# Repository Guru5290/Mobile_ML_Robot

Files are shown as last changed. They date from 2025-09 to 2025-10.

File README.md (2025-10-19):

Project for [Robotics Dojo 2025](https://roboticsdojo.github.io/competition2025.html). A few mods to Josh Newans' articubot_one project documented on [github](https://github.com/joshnewans/articubot_one) and [youtube](https://www.youtube.com/playlist?list=PLunhqkrRNRhYAffV8JDiFOatQXuU-NnxT). 

# Quick Links
* [Sources](#sources)
* [Hardware Configuration](#hardware-configuration)
* [Software Dependencies](#software-dependencies)
* [Modified Parameters](#modified-parameters)
    * [Note](#note)
    * [Note on Localization](#note-on-localization)
* [Usage](#usage)
    * [Prerequisites](#preliminary)
    * [Simulation](#simulation)
    * [Real Robot](#real-robot)
    
* [Misc.](#misc)
* [Future](#future)

# Sources
- Simulation world obtained from the stl file sent by Lenny Ng'ang'a by converting it to a COLLADA file and importing it in Gazebo Fortress then saving it with the robot spawned in it. `src/jkl/worlds/GF.sdf`
- Map evaluation script obtained from [Dr. Shohei Aoki's repo](https://github.com/shohei/Map_Evaluation)
- diffDriveArduino from [RedstoneGithub's fork](https://github.com/RedstoneGithub/diffdrive_arduino) of Josh's diffdrive arduino
- [sllidar](https://github.com/Slamtec/sllidar_ros2) and [rplidar](https://docs.ros.org/en/ros2_packages/humble/api/rplidar_ros/) from those links
- [joy tester](https://github.com/joshnewans/joy_tester) is from Josh
- [serial](https://github.com/joshnewans/serial) is from Josh
- [serial_motor_demo](https://github.com/joshnewans/serial_motor_demo) is from Josh
- [rosArduinoBridge](https://github.com/joshnewans/ros_arduino_bridge) is Josh's fork of [hrobotics work](https://github.com/hbrobotics/ros_arduino_bridge)
  
Our [technical design paper](Technical%20paper%20Team_1%20Knights%20RDJ%202025.pdf), [technical presentation slides](Robotics%20Dojo%202025%20Knights%20Presentation.pdf), and [project poster](knights_poster%20RDJ%202025.pdf) may have a few more details on this project.

# Hardware Configuration
- Raspberry Pi running Ubuntu 22.04, dev machine running Ubuntu 22.04
- RPLidar A1 M8 connected to Pi via USB
- STM32F401 running [ROSArduinoBridge.ino](arduino-code/ROSArduinoBridge/ROSArduinoBridge.ino), connected to Pi USB
- 4 200 RPM motors with built-in encoders, with the encoders connected as shown in [encoder_driver.h](arduino-code/ROSArduinoBridge/encoder_driver.h)
- DRV8833 motor driver, with motor controls connected as shown in [motor_driver.h](arduino-code/ROSArduinoBridge/motor_driver.h)
- MPU6050 over I2C. The arduino sketch enables the DMP for great IMU performance. Also, a calibration sketch is provided by the [electronic cats library](https://github.com/ElectronicCats/mpu6050/wiki). This improved accuracy greatly.
- MG996R servo motor for bed actuation

Here's the bot [here](1L9A4192.JPG), [here](IMG_6601.jpeg)
Here's a simple  overview of the circuit. 
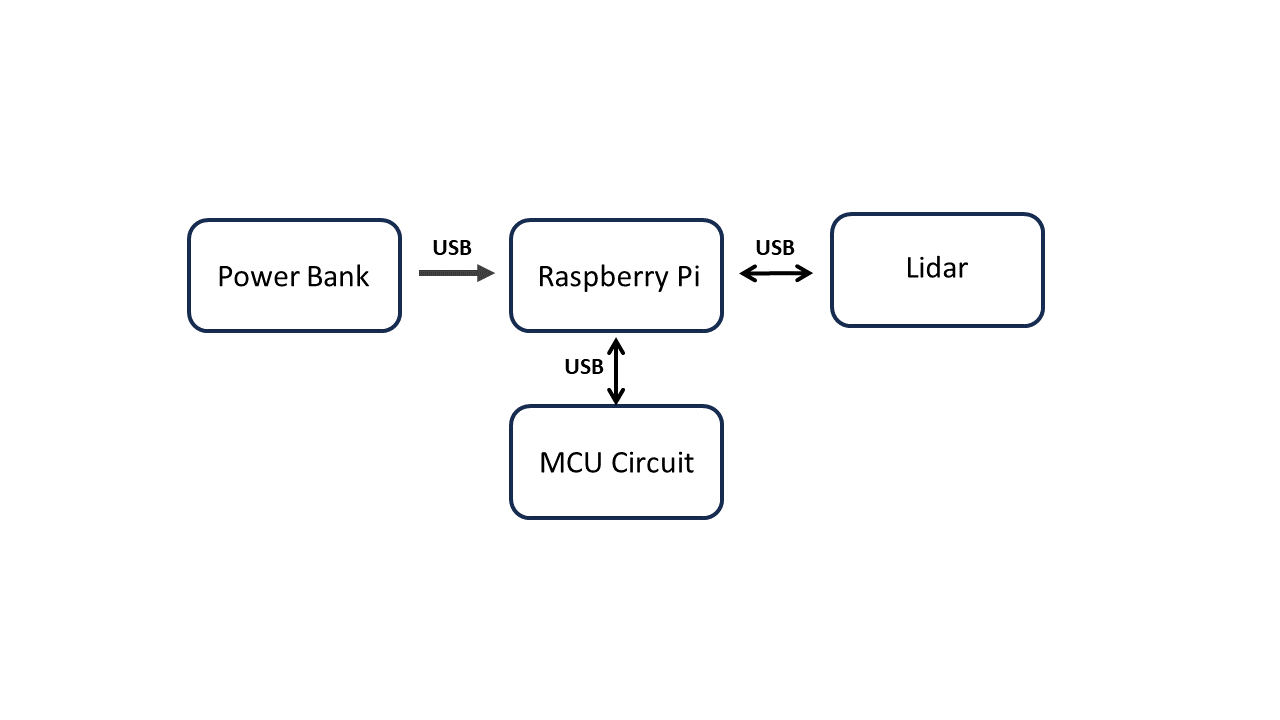
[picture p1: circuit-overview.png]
circuit overview


[This pdf](MCU-circuit.pdf) shows the MCU circuit in detail. The STM32 ships with a USB bootloader, allowing programming using DFU over usb. The configuration used in Arduino IDE is as below, STM32 boards can be added using this URL [https://github.com/stm32duino/BoardManagerFiles/raw/main/package_stmicroelectronics_index.json](https://github.com/stm32duino/BoardManagerFiles/raw/main/package_stmicroelectronics_index.json):
```
board manager entry - STM32 Based Boards by STMicroelectronics 
board - generic stm32f4 series
board part number - blackpill F401CC
Upload method - STM32Cube DFU
USB support - generic CDC Serial supercede U(S)ART
```

It is important to avoid using pins PA8-PA12. They're shown in blue on [the pinout diagram](STM32F401-pinout.jpg). These 5 pins have USB alternate functions and so misbehave when used as GPIO. Emphasis on PA11 (USB D-) and PA12 (USB D+). If you somehow get stuck unable to program the MCU over USB, you can recover by uploading a blank sketch using an FTDI, or ST-Link. 

# Software Dependencies
- Ubuntu 22.04 - ROS2 Humble pair was used here. Docker on windows is not recommended by us because of network woes. The WSL network is isolated from the system network, so ROS on Pi does not communicate with ROS on Docker by default. We were not able to get it working in time. Apart from that, native Ubuntu has way higher performance.
- twist-mux, ros-humble-teleop-twist-keyboard, ros-humble-teleop-twist-joy, slam-toolbox, ros-humble-navigation2, ros-humble-nav2-bringup, ros-humble-gazebo-ros-pkgs, ros-humble-xacro, ros-humble-ros2-control, ros-humble-rplidar-ros, ros-humble-robot-localization
<!-- - ros-humble-gazebo on pc -->
- tmux is not recommended, it was laggy on the Pi over SSH over wifi

# Modified Parameters
## src/jkl/description
### robot.urdf.xacro
The URDF was built using simple shapes. URDF using meshes was attempted [see knight.xacro](pi-code/src/jkl/description/urdf/knight.xacro). The benefit was the mesh was derived from the actual CAD of the robot. However, it was too laggy to update pose, etc. It was suspected that computing collisions using meshes was the cause, hence the creation of the [current URDF](pi-code/src/jkl/description/urdf/simple.xacro). 

Important to note is that the IMU on the actual robot was mounted such that X and Y axes did not match the X and Y axes of the robot. Also please note that for this manufacturer the axes drawn on the module are actually -X and -Y. Verify with your IMU's raw data if you plan to replicate this

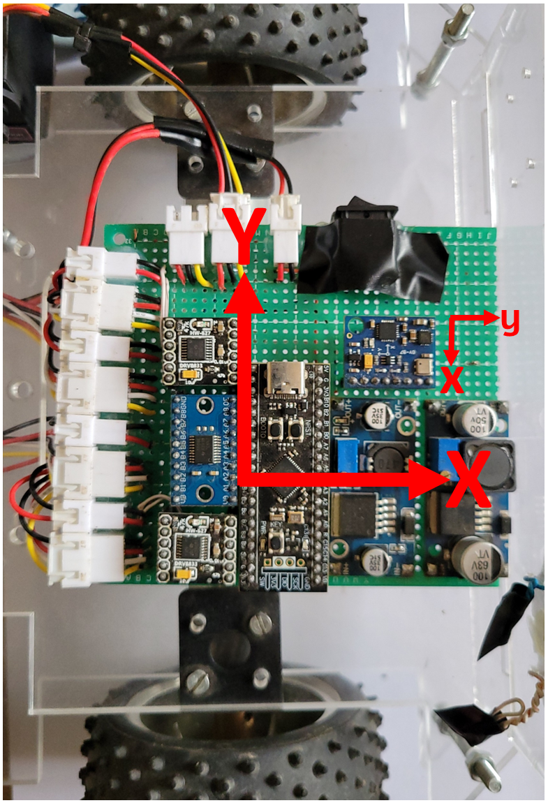
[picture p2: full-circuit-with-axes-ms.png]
full circuit with axes


So in the URDF, the IMU was rotated about the Z axis to match. This also affects the [EKF configuration file](#ekfyaml): we fuse the Y acceleration instead of X because Y is our axis of interest i.e. robot-forward axis. A justifiable assumption is that the imu_link->...->base_link TF's would account for this behind the scenes with the robot_localization package but no it does not at the time of writing. 
Had this been foreseen, the IMU would have been mounted x on X and y on Y. 

The URDF features an offset value for the centre of rotation. When the robot spins in place, it rotates about `base_link` (because the odom TF is odom->base_link). Therefore, it is important to match the centre of rotation of the real robot (or gazebo simulated robot) with the centre of rotation in Rviz. That's the role of `centre_of_rot_offset_x`. Getting this value right greatly improves odometry: when you set the fixed frame to odom in rviz, the laser frame will not drift. 

### gazebo_control.xacro (although not used)
```xml
<wheel_separation>0.207</wheel_separation>
<wheel_radius>0.0425</wheel_radius>
```

### ros2_control.xacro
```xml
<!-- stm32 -->
<param name="device">/dev/serial/by-id/usb-STMicroelectronics_BLACKPILL_F401CC_CDC_in_FS_Mode_206734803156-if00</param> 
<param name="baud_rate">57600</param>
<param name="enc_counts_per_rev">988</param>
```

## src/jkl/config/
### mapper_params_online_async.yaml
```yaml
loop_search_maximum_distance: 6.0 # (default is 3.0). The default value causes the robot to "teleport" during mapping, ruining a good map
```

### nav2_params.yaml
- initial_pose (not defined by default). Helps save time when using localization. A new pose can be given using rviz. Use it by having the odom reset (relaunching launch_robot) then launching online_async.launch.py. Then set the initial pose as 0 0 0
- controller_server: [mppi controller server](https://docs.nav2.org/configuration/packages/configuring-mppic.html) was used (dwb is default). rpp, teb and grace might have worked better, but mppi worked best out of the box
- controller server loop rate 15 Hz to minimize console spamming "control loop missed its 30Hz update rate"
- local_costmap & global_costmap: resolution: 0.02 (0.05 is default). Seems to get robot get stuck less frequently
- local_costmap: footprint used instead of radius, coz the robot is a polygon. Sized just over the robot's size
- global_costmap: radius retained, perhaps less compute intensive than footprint?
- amcl laser_max_range and min_range 12.0 and 0.3 respectively (default is )
- velocity smoother feedback: "CLOSED_LOOP" (default is OPEN_LOOP)
- velocity smoother velocities and accelerations: [0.35, 0.0, -0] and [12.5, 0.0, 8.2] (default are something else) The accelerations are very large. Something better should be identified and used
- [The docs](https://docs.nav2.org/tuning/index.html#inflation-potential-fields) recommends inflation radii that create **smooth** potential fields in the global and local costmaps. However, in testing, it was observed that having overlapping potentials (such as on corridors and parking spots) would cause the robot to fail passing as expected, even though a path had been planned. So the inflation radii were reduced until there was a little empty space in both costmaps at the narrowest corridor of the gamefield. 

We tried using the [theta-star planner](https://docs.nav2.org/configuration/packages/configuring-thetastar.html) instead of the default navfn. The robot plans are shorter and straighter, fixing the weaving issue we had last year. However, the plans hug the inflation radius too closely, causing navigation around simple corners to fail in a manner similar to that observed when the potential fields overlap. With time, perhaps that can be tuned out?

### my_controllers.yaml
For diff_cont
```yaml
wheel_separation: 0.207
wheel_radius: 0.0425
wheels_per_side: 2
odom_frame_id: odom
enable_odom_tf: false # crucial for EKF
```

These fields were added to provide hardware interfaces to the servo and IMU and 2 more wheels
```yaml
controller_manager:
  ros__parameters:
    # existing diff_cont

    # joints doubled for joint_broad
    joint_broad:
      type: joint_state_broadcaster/JointStateBroadcaster
      joints: ['front_left_joint', 'front_right_joint', 'back_left_joint', 'back_right_joint']
    
    imu_broadcaster:
      type: imu_sensor_broadcaster/IMUSensorBroadcaster # https://control.ros.org/humble/doc/ros2_controllers/imu_sensor_broadcaster/doc/userdoc.html

    servo_controller:
      type: position_controllers/JointGroupPositionController # https://control.ros.org/humble/doc/ros2_controllers/position_controllers/doc/userdoc.html

imu_broadcaster:
  ros__parameters:
    sensor_name: imu_sensor # specified in HW interface
    frame_id: imu_link

servo_controller:
  ros__parameters:
    joints:
      - servo # specified in HW interface
```

It is critical that enable_odom_tf in diff_cont should be false because ros2_control should not publish the odom->base_link transform. That role should be done by the EKF node. 

### ekf.yaml
[This config file](pi-code/src/jkl/config/ekf.yaml) is for sensor fusion using the [robot_localization](https://docs.ros.org/en/noetic/api/robot_localization/html/configuring_robot_localization.html) package. The configuration was largely based on the DOCS with one difference: The IMU on the robot was rotated 90 degrees about X axis wrt to the robot axes. So in order to fuse the acceleration along X axis, we actually fuse the reported acceleration of Y axis. 
#### Notes
* `publish_tf` is true. This is because ros2_control is no longer publishing the tf. 
* `imu0_relative` is true. We are only interested in the change in angular rotation about Z, not absolute angle value. Otherwise the orientation in RVIZ will be inconsistent per-run
* `imu0_remove_gravitational_acceleration` is true, the IMU reports absolute accelerations without subtracting gravity

## src/jkl/launch/
### rplidar.launch.py
The rplidar_ros launch file for A1 was copied and these fields were modified
```python
serial_port = LaunchConfiguration('serial_port', default='/dev/serial/by-id/usb-Silicon_Labs_CP2102_USB_to_UART_Bridge_Controller_0001-if00-port0') # was '/dev/ttyUSB0'
serial_baudrate = LaunchConfiguration('serial_baudrate', default='115200')
frame_id = LaunchConfiguration('frame_id', default='laser_frame') # was 'laser'
```

## [diffdrive_arduino](pi-code/src/diffdrive_arduino/)
Hardware interfaces for 2 additional wheels, servo and IMU were added. The serial commands for the latter two were added both in this package and in ROSArduinoBridge. Check out [arduino comms](/pi-code/src/diffdrive_arduino/src/arduino_comms.cpp), [arduino_comms.cpp](/pi-code/src/diffdrive_arduino/src/arduino_comms.cpp), [diffdrive_arduino.cpp](/pi-code/src/diffdrive_arduino/src/diffdrive_arduino.cpp), and their .h files for more info. 

Note that the state interface for the servo is not implemnted based on the reported servo angle. Instead, it is reported using the previously commanded angle. Although the command is provided in the arduino sketch, at the time, it was more important to prevent frequent checks on the servo position rather than prioritizing fetching the wheel encoder data. So the command interface only sent commands to the MCU if a different angle command was sent. 

This choice created some buggy behaviour with the servo. If launch_robot was executed while the servo was in the open position, publishing [170.0] to the `servo_controller/commands` topic would not close it. So you would have to "open it" using [90.0] first then it would close. There was also a bug where publishing an angle command to the topic only once would have no effect. As of yet, unclear if this is also related. 

A future implementation would definitely update state variable as it should be. 

Check out [diffdrive_arduino.cpp](pi-code/src/diffdrive_arduino/src/diffdrive_arduino.cpp) and its .h file

## Note
- Josh goes over how to obtain wheel diameter, wheel separation and encoder counts per revolution in [this video](https://www.youtube.com/watch?v=4VVrTCnxvSw&list=PLunhqkrRNRhYAffV8JDiFOatQXuU-NnxT)
- **online_async_launch.py** **localization_launch.py**, **navigation_launch.py**, **mapper_params_online_async.yaml**, **nav2_params.yaml** were copied from the default slam-toolbox and nav2_bringup directories (/opt/ros/humble/share/nav2-or slam-toolbox...) then slightly modified (for example in localization_launch.py instead of `get_package_share_directory('nav2_bringup')` use `get_package_share_directory('jkl')`) This is the recommended way to do it because, Josh's articubot_one repo uses ROS foxy. Apart from fewer parameters in nav2 and mapper yaml, some problems might come up like failing to launch navigation. Some elements were renamed in ROS Humble, like recoveries->behaviors
- all instances of serial ports use `dev/serial/by-id` path. This was preferred over `dev/serial/by-path` and `dev/tty*` because it depends on the device ID rather than the port used or connection order
- Electronic cats provides a [calibration sketch](https://github.com/ElectronicCats/mpu6050/wiki/4.-Examples#zero) for the IMU. This improved accuracy greatly. 

## Note on Localization
In testing, it was noted that localization using AMCL (the default for Nav2) was unsatisfactory. The map and laser scan would go out of alignment very quickly, causing navigation to fail. A few attempts were made to tune the [parameters](/pi-code/src/jkl/config/nav2_params.yaml) using [this guide](https://automaticaddison.com/ros-2-navigation-tuning-guide-nav2/) but the performance was still sub-par. A little research showed **many** others shared our discontent and so provided promising alternatives to AMCL:
1. jie_ware youtube [here](https://youtu.be/sZ5_NEt1vI4?si=0gPA8b-hRr3kHton) and github [here](https://github.com/6-robot/jie_ware) ROS1 :(
2. als_ros youtube [here](https://youtu.be/wsoXvUgJvWk?si=MrWsakbt202Rw9hv) and github [here](https://github.com/NaokiAkai/als_ros) ROS1 :(
3. WLOC youtube [here](https://youtu.be/ik6-cSJZV1k?si=ls9vA8XfLilKkfMt) no source could be found :(
4. rtabmap github [here](https://github.com/introlab/rtabmap/tree/humble-devel) huge and reportedly high compute requirements :( However, it supports mapping with stereo RGB-D cameras, 3D lidar, and [a lot more](https://github.com/introlab/rtabmap/wiki/Tutorials)
5. GMCL youtube [here](https://youtu.be/J9ZcCon6k-g?si=GTzK6mh_Yn7lSSTg) and github here
6. neo_localization github [here](https://github.com/neobotix/neo_localization2/tree/humble) docs [here](https://neobotix-docs.de/ros/packages/neo_localization.html)

We only tested neo_localization and jie_ware. Neo_localization was just a drop-in replacement for AMCL, but was indistinguishable from it. Perhaps with a little more tuning and consideration, it could be ironed out. 

Jie_ware was written for ROS1. After a little effort to port it to ROS2, we found it to be very aggressive, exactly what we wanted. We could have tested the others but they either required a lot more effort to integrate. Jie_ware only had 3 source files

# Usage
## 
- Wifi (or ethernet) has to be connected, on both pi and PC whenever you're running ROS, especially if using cyclone DDS as the RMW_IMPLEMENTATION
## Preliminary
- [install ros-humble](https://docs.ros.org/en/humble/Installation/Ubuntu-Install-Debs.html)
- add `source /opt/ros/humble/setup.bash` to ~/.bashrc so you don't have to in every new terminal
- install [nav2, slam-toolbox](https://roboticsbackend.com/ros2-nav2-generate-a-map-with-slam_toolbox/), colcon, and optionally [change RMW_IMPLEMENTATION to cyclone_dds](https://roboticsbackend.com/ros2-nav2-generate-a-map-with-slam_toolbox/)
- install controllers, plugins, xacro and twist mux 
```bash
sudo apt install ros-humble-ros2-control ros-humble-ros2-controllers && \
# sudo apt install ros-humble-gazebo-ros2-control && \ # Gazebo Classic went EOL so this won't work, make migration
# sudo apt install ros-humble-gazebo-ros-pkgs && \ 
sudo apt install ros-humble-xacro && \
sudo apt install ros-humble-twist-mux && \
sudo apt install ros-humble-slam-toolbox && \
sudo apt install ros-humble-navigation2 ros-humble-nav2-bringup && \
sudo apt install ros-humble-robot-localization && \
sudo apt install ros-humble-rplidar-ros && \
```
- disable brltty service. This service always takes serial port devices to be braille device, preventing you from accessing your microcontroller. Disable the service
```bash 
systemctl stop brltty-udev.service && \
sudo systemctl mask brltty-udev.service && \
systemctl stop brltty.service && \
systemctl disable brltty.service
```
- enable read/write to serial port, you can do this by adding yourself to the dialout group `sudo usermod -a -G dialout $USER` **then reboot**
- clone the repository in both Pi and dev machine
- cd to the location of src directory in both Pi and dev machine e.g. `cd ~/robotics-dojo-2024/pi-code`
- edit pi-code/src/jkl/description/ros2_control.xacro line 11 to the appropriate for your microcontroller. You can check which is appropriate by connecting the microcontroller to your machine then running `ls /dev/serial/by-id`. You can then add it as appropriate
- run `colcon build --symlink-install` in both Pi and dev machine. It may throw a lot of errors and/or warnings on first build, just ignore and run `colcon build --symlink-install` again. This should be fixed in future versions of this project.
- run `source install/setup.bash` on each terminal (or add `source yourworkspace/install/setup.bash` to ~/.bashrc) in both Pi and dev machine

## Simulation
Everything is run on pc. Instead of running `ros2 launch jkl launch_robot.launch.py` **and** `ros2 launch jkl rplidar.launch.py`, use `ros2 launch jkl launch_sim.launch.py use_sim_time:=true world:=./src/jkl/worlds/dojo2024` 
Change every instance of `use_sim_time:=false` to `use_sim_time:=true`
All else is as below

## Real Robot
- cd to the location of src directory in both Pi and dev machine e.g. `cd ~/robotics-dojo-2024/pi-code`
- On PC run `rviz2 -d ./src/comp.rviz`
- On Pi, run `ros2 launch jkl launch_robot.launch.py`
- On Pi in another terminal run `ros2 launch jkl rplidar.launch.py`. You may also use `ros2 launch rplidar_ros rplidar_a1_launch.py` or `ros2 launch sllidar_ros2 sllidar_a1_launch.py`. In a few tests, we noticed that the latter two run at 8kHz, instead of the former's 2kHz. Also, these launch files show the lidar is in `Sensitivity` mode rather than `Standard` mode. We're not sure if there are benefits in using these two over Josh's. 

### For mapping phase
- On PC (Pi is also fine but during competition we found PC was better, did not have the "teleportation" issue) run `ros2 launch jkl online_async_launch.py slam_params_file:=./src/jkl/config/mapper_params_online_async.yaml use_sim_time:=false`
- On PC or Pi run `ros2 run teleop_twist_keyboard teleop_twist_keyboard`
- you may also use gamepad instead of keyboard, but you'll have to configure the joystick yaml appropriately. Josh demonstrates the process well [here](https://www.youtube.com/watch?v=F5XlNiCKbrY&list=PLunhqkrRNRhYAffV8JDiFOatQXuU-NnxT&index=17). But in short run `ros2 run joy joy_node` in one terminal then `ros2 run joy_tester test_joy` in another. Press a key, identify its id using the GUI and use that id in the jkl/config/joystick.yaml. Having configured the yaml correctly, you can use `ros2 launch jkl joystick.launch.py` in place of or in conjuction with teleop_twist_keyboard. joystick **does not** require its terminal window to be in focus to work
- With the teleop_twist_keyboard terminal in focus use `u i o j k l m , .` to drive the bot around until a satisfactory map is shown in rviz
- Open slam toolbox panel in rviz and fill the input boxes with a desired name. Click save map and serialize map. Four map files will be saved in current directory

### For navigation phase
- (on pc or pi, but pc is more powerful) You may use slam_toolbox or localization_launch for localization. slam_toolbox is not recommended since it (currently) overwrites (or updates) the existing map with new scans. If you wish to proceed anyway, this is how you do it: change `mode: mapping` to `mode: localization` and uncomment `map_file_name:` followed by path to the **serialized** map file (i.e. the file that has .data or .posegraph extension), without extension, in src/jkl/config/mapper_params_online_async.yaml. Then run same command as when mapping `ros2 launch jkl online_async_launch.py slam_params_file:=./src/jkl/config/mapper_params_online_async.yaml`.
- To use localization_launch (AMCL localization), kill online_async if it was running then run  `ros2 launch jkl localization_launch.py map:=path_to_map.yaml use_sim_time:=false`. To set/change pose estimate, you can use rviz
- To use jie_ware localization package: [jie_ware](pi-code/src/jie_ware/)

The **jie_ware** package provides advanced **LIDAR-based localization** capabilities. It allows the robot to automatically localize itself within its operational area using **only lidar data** and the map, making it highly suitable for autonomous navigation and mapping tasks. That means the odometry need not be precise, or even remotely accurate as [some](https://www.reddit.com/r/ROS/comments/1iwslhb/amcl_alternatives_found_a_lightweight_lidaronly/) have used it with a **static!** odom->base_link TF without trouble. 

This package was originally developed for **ROS 1** and is available here:  
 [https://github.com/6-robot/jie_ware](https://github.com/6-robot/jie_ware)  
It has been successfully **ported to ROS 2** for integration with this project.

---

###  Running the Localization Node
To use **jie_ware** localization, run the following command:

```bash
ros2 launch jie_ware lidar_loc.launch.py map:=<map_name>.yaml use_sim_time:=false
```

Replace `<map_name>.yaml` with the desired map file that you have saved.

When running, the robot will automatically localize itself if it is within its known mapped area.

---

###  Demo Video
A demonstration of the **jie_ware localization** package can be found here:

 [Watch on YouTube](https://youtu.be/sZ5_NEt1vI4?si=CmsiGj_6Rxt5UtrA)

---

###  Key Features
- Automatic localization within known mapped environments
- LIDAR-based positioning for accuracy and robustness
- Compatible with ROS 2 navigation stacks
- Fully ported from ROS 1 for better performance and integration
### Running navigaton

* **(On PC or Raspberry Pi — though PC is recommended due to the Pi’s computational limitations)** run the following command to launch navigation:

  ```bash
  ros2 launch jkl navigation_launch.py map_subscribe_transient_local:=true params_file:=./src/jkl/config/nav2_params.yaml use_sim_time:=false
  ```

* Instead of using the RViz navigation plugin to set waypoints, **PyTrees** was adopted, following Dr. Aoki’s tutorial: [PyTrees Navigation Tutorial](https://youtu.be/EqSgKu8-xEU?si=lQmXRzx3Bd9OWw90).

* The script `pi-code/src/nav_to_poses/nav_to_poses/nav_to_poses.py` was used to execute the navigation tasks defined in the YAML configuration file:

  ```
  pi-code/src/nav_to_poses/nav_to_poses/config/nav_goals.yaml
  ```

* After launching navigation, the script was executed using:

  ```bash
  ros2 run nav_to_poses nav_to_poses
  ```

* Tasks requiring external script execution from within `nav_to_poses.py` were handled using Python’s `subprocess.run()` method, as described in the [official documentation](https://docs.python.org/3/library/subprocess.html).

* For full autonomy, the **Raspberry Pi Camera 2 (picamera2)** stream was continuously active on the Raspberry Pi. Frames were captured on-demand for specific tasks, including **potato leaf disease detection** and **colour detection** of the white and blue cubes.

## Computer Vision

## [rdj2025_potato_disease_detection](pi-code/src/rdj2025_potato_disease_detection/)

###   Project Overview
This package is part of a computer vision system for detecting **potato leaf diseases** using **deep learning** on a **ROS 2** framework. It supports both **RTSP-based live camera feeds** from a Raspberry Pi Camera Module 2 and **locally saved test images**. The model can classify potato leaf conditions and display the confidence level of each prediction as either early blight, late blight or healthy.

---

###   Requirements / Dependencies
Before running, ensure the following are installed:

- **Hardware:** Raspberry Pi (with Camera Module 2 - IMX219)
- **Operating System:** Raspberry Pi OS or Ubuntu 22.04 (with ROS 2 Humble)
- **Dependencies:**
  - Python 3.10+
  - ROS 2 (installed and sourced)
  - OpenCV (`opencv-python`)
  - PyTorch (`torch`, `torchvision`)
  - FFmpeg (for video streaming)
  - rpicam-vid (camera streaming utility)

Install missing dependencies via:

```bash
sudo apt install ffmpeg
pip install torch torchvision opencv-python
```

---

###   Start Raspberry Pi Camera Stream
Before running the required nodes, ensure the **Raspberry Pi Camera Module 2** is streaming using:

```bash
rpicam-vid -t 0 --nopreview --inline --codec mjpeg --width 1920 --height 1080 \
--framerate 10 --hflip --vflip --awb daylight --autofocus-mode manual \
-o - | ffmpeg -f mjpeg -i - -c:v copy -f rtsp -rtsp_flags listen rtsp://0.0.0.0:8554/cam
```

You may modify parameters such as autofocus or white balance, but these defaults provided stable results.

  **Reference:** [Raspberry Pi Camera Software Documentation (IMX219 V2)](https://www.raspberrypi.com/documentation/computers/camera_software.html)

---

###  Running the ROS 2 Nodes
To run the two nodes, open separate terminals and execute:

1. **Potato Disease Detection Node:**
   ```bash
   ros2 run rdj2025_potato_disease_detection potato_disease_detection_node
   ```

2. **Image Publisher Node:**
   ```bash
   ros2 run rdj2025_potato_disease_detection publish_test_image
   ```

The second node can be configured in `setup.py` to switch between **RTSP streaming** or **local images**.

---

###  Node Locations
- Detection Node:  
  `pi-code/src/rdj2025_potato_disease_detection/rdj2025_potato_disease_detection/potato_disease_detection_node.py`

- RTSP Image Publisher:  
  `pi-code/src/rdj2025_potato_disease_detection/rdj2025_potato_disease_detection/rtsp_image_publisher.py`

- Test Image Publisher (Local):  
  `pi-code/src/rdj2025_potato_disease_detection/rdj2025_potato_disease_detection/test_image_publisher.py`

---

###  Model Details
- **Commented code** in the following files uses the model trained by **RDJ 2025 organizers**:
  - `inference_engine.py`
  - `potato_disease_detection_node.py`

    Repository: [https://github.com/roboticsdojo/rdj2025_potato_disease_detection](https://github.com/roboticsdojo/rdj2025_potato_disease_detection)

- **Uncommented sections** use the custom model trained by this team:
  - `pi-code/src/rdj2025_potato_disease_detection/models/potato_disease_model.pth`

This custom model achieved higher accuracy and provided classification confidence levels for each prediction.

## Colour Detection

## [colour_door_controller](pi-code/src/colour_door_controller/)

This package is part of the **Computer Vision** system and controls a **servo-driven door mechanism** based on detected colours from a live RTSP video stream.

---

###  Overview
The package contains two main nodes:

1. **Colour Detector Node** – Publishes the detected colour from the RTSP stream.  
   Location: `pi-code/src/colour_door_controller/colour_door_controller/colour_detector.py`

2. **Colour to Door Service Node** – Controls the servo motor based on the detected colour (supports **blue** and **white**).  
   Location: `pi-code/src/colour_door_controller/colour_door_controller/colour_to_door_service.py`

These nodes together enable a door automation mechanism that responds to specific colour detections in real-time.

---

###  Prerequisites
Before running these nodes, ensure that the **Raspberry Pi Camera Module 2** is streaming using the following command:

```bash
rpicam-vid -t 0 --nopreview --inline --codec mjpeg --width 1920 --height 1080 \
--framerate 10 --hflip --vflip --awb daylight --autofocus-mode manual \
-o - | ffmpeg -f mjpeg -i - -c:v copy -f rtsp -rtsp_flags listen rtsp://0.0.0.0:8554/cam
```

You may modify the camera parameters (e.g., white balance, autofocus), but the above configuration is recommended for best performance.

---

###  IP Configuration
To ensure proper RTSP streaming, verify that **all instances of the IP address** in the scripts match your Raspberry Pi's IP address.

In VS Code, you can search for all IP instances using:
```
Ctrl + Shift + F
```

Alternatively, you can pass the IP as a runtime parameter when launching the detector node:

```bash
ros2 run colour_door_controller colour_detector --ros-args -p IP:=<your_IP>
```

---

###  Running the Nodes
1. **Run the Colour Detector Node:**
   ```bash
   ros2 run colour_door_controller colour_detector
   ```

2. **Run the Colour to Door Service Node:**
   ```bash
   ros2 run colour_door_controller colour_to_door_service
   ```

These two nodes will work together — the detector identifies the colour (blue or white), and the service node controls the servo motor accordingly.

---

### Notes
The current implementation is a little biased toward white detection. A gentle blur before processing might help. 

# Misc.
- the lidar sometimes acts up when attempting to launch. If it fails to launch even after mutliple retries, (1) try **unplug and replug** connections, i.e., usb connection on pi, usb on lidar, the lidar daughter board cables, other daughter board cable motor side and laser side, you get the idea (2) try using a different type-c cable, or different power supply altogether for the raspberry pi. This was an issue in 2024 but not 2025.
- Update on above issue: Josh posted [a video](https://youtu.be/PddIeZP-wgw?si=uCTXcbRP3fAoC-ss) about power supplies for Pi. He suggested this change as one fix at timestamp 5:45.
```bash
sudo rpi-eeprom-config --edit
```
A file will open with nano-like editor. Add this line to it
```
PSU_MAX_CURRENT=5000
```
Tried 3000 (coz its Pi 4), Josh tried 4000 on his Pi 5 but it would not work in both cases, even though it seemingly should. But 5000 seems a little reliable for both. 
- you can save changes to comp.rviz (or the default rviz config) when you hit Ctrl+S so that you don't have to make the same changes when relaunching rviz
- for simulations, slow computers may produce unrealistic navigation behaviours, like aborting too soon. Gazebo is a resource hog. So try to launch launch_sim in one pc then everything else in another pc configured in the same way, connected in the same network 
- use float where float is used in yaml files, otherwise stuff may fail to launch
- sometimes things don't work very well, relaunch and reboot are a must for both Pi and PC
- rplidar.launch.py sometimes takes a few tries to get working, also try disconnecting arduino then launch lidar first
- use `export ROS_DOMAIN_ID=some-number-that-is-not-the-default-0` per terminal or in bashrc to avoid communicating with other people's ROS environments. Do this for both your PC and PI
- cyclonedds is recommended over fastrtps because ["it doesn't work well with nav2"](https://roboticsbackend.com/ros2-nav2-tutorial/). Install using `sudo apt install ros-humble-rmw-cyclonedds-cpp` and then per terminal or in bashrc `export RMW_IMPLEMENTATION=rmw_cyclonedds_cpp`
- Raspberry running ubuntu 22.04 sometimes takes a long time to boot. Using `systemd-analyze blame`, it seems to be caused by `systemd-networkd-wait-online.service`. A workaround is turning `optional` to `false` in `/etc/netplan/50-cloud-init.yaml`. A better fix should be identified. 

# Future
- Fix weaving. When the path is relatively straight the robot follows a winding path, it weaves left and right, which might cause it to hit an obstacle. In the competition, we reduced the maximum angular velocity to work around this.
- Make the robot smaller (particularly wheel_separation), like [Atom x RoboQueens robot](atom-roboqueens-robot.png)  ---> ✔️
- Isolate the arduino and motor driver, tristate buffer and/or relay? 
- Find a way to power lidar motor properly. Why was the USB hub buzzing when switched on? Modify a USB cable, so that an additional power cable is soldered to the 5V line, for simplicity and compactness
- Get a really good USB PD power bank for the Raspberry Pi
- Get USB-C trigger boards, or build battery pack with BMS to avoid overdischarging motor power supply like last time
- Wifi sucks. Check if you can get a better AP or ditch wifi altogether and use thin ethernet cable
- Try increasing rates (like decreasing map update interval, increase controller frequency, map publish rates, robot velocities etc) in mapper params and nav2 params
- Try [RPP](https://docs.nav2.org/configuration/packages/configuring-regulated-pp.html#), TEB, [Graceful](https://docs.nav2.org/configuration/packages/configuring-graceful-motion-controller.html) and [DWB](https://docs.nav2.org/configuration/packages/configuring-dwb-controller.html) controller servers (with and without [rotation shim](https://docs.nav2.org/configuration/packages/configuring-rotation-shim-controller.html))
- Restore the original ISR in ROSArduinoBridge using the newfound knowledge in register operations. Should have a small speed boost.
- Try using a differert fork of supporting packages (like serial and serial motor demo) because the ones used have easy_install deprecation warnings during colcon build --symlink-install
- Try using very high resolution laser scan and local and global costmaps to see if the bot ever gets stuck (without modifying robot radius that is)
- Try a different path planner, like [smac](https://docs.nav2.org/configuration/packages/configuring-smac-planner.html) or [thetastar](https://docs.nav2.org/configuration/packages/configuring-thetastar.html), maybe they will perform better with higher resolution costmaps. When thete-star was tested with resolution 0.05, generated paths were straighter and often passing through the robot radius regions hence the robot would get stuck in recovery easily. It also fixed the weaving issue mentioned earlier in this section. Also explore effect of deadband velocity, as well as other params n this file.
- Try and use `ros2 launch sllidar_ros2 sllidar_a1_launch.py` or `ros2 launch rplidar_ros rplidar_a1_launch.py` instead of jkl rplidar.launch.py to see if the 8kHz and 'Sensitivity' vs 2kHz and 'Standard' makes it better ---> ✔️ Used `ros2 launch rplidar_ros rplidar_a1_launch.py frame_id:=laser_frame`
- Try using a different bt_navigator xml such as the ones in jkl/config/behavior_trees. You specify the one to use in nav2_params.yaml
- Explore effect of other params in my_controllers.yaml. There's also closed-loop there, might be valuable
- Make the mapping phase also autonomous
- Incorporate IMU, maybe this has benefits ---> ✔️
- Try depth camera instead of lidar
- Make a simple BMS, can add a simple MOSFET switch to prevent overdischarge from battery. Can also configure battery pack to be able to charge using LiPo charger, something like 3s 2p config?
- a guest on Tech Expo said we should check AWS Deepracer 
- Maybe explore [Ackermann](https://en.wikipedia.org/wiki/Ackermann_steering_geometry) steering? with 4WD and ability to use diffdrive in tight spots :)
- Have an mini PC as part of the robot to run all needed software to do away with WIFI & Hotspot problems during the competition. Maybe this might do [HP EliteDesk 705 G4 Microtower PC - Ryzen 5 Pro 2400GE 3.2GHz, 8 CPUs, 8GB RAM, 256GB NVMe M.2 SSD, Radeon RX Vega 11 Graphics, DP, Gigabit LAN](https://bestsella.co.ke/product/hp-elitedesk-705-g4-microtower-pc-ryzen-5-pro-2400ge-3-2ghz-8-cpus-8gb-256gb-nvme-m-2-ssd-radeon-rx-vega-11-graphics-dp-gigabit-lan/), Minisforum [EM680](https://www.youtube.com/watch?v=2nI25tk-NMM)?
- Add Apriltag for precise docking/parking

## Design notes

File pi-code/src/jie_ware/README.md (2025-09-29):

# 阿杰的 ROS 工具箱

## 视频介绍

Bilibili: [《一种简单易用的激光雷达定位方法》](https://www.bilibili.com/video/BV1fB29YzEgP/)  
Youtube: [《一种简单易用的激光雷达定位方法》](https://www.youtube.com/watch?v=0JqGX8lKRu0)  
Bilibili: [《代价地图清除》](https://www.bilibili.com/video/BV1kwzqYyEe7/)  
Youtube: [《代价地图清除》](https://www.youtube.com/watch?v=giHf_PY4EmY)  
Bilibili: [《去除ROS导航中的激光雷达噪点》](https://www.bilibili.com/video/BV1LFjBzREQu)  
Youtube: [《去除ROS导航中的激光雷达噪点》](https://www.youtube.com/watch?v=98GF6_zN_IA)  
基础：[《ROS 快速入门教材》](https://www.bilibili.com/video/BV1BP4y1o7pw/)  
扩展：[《ROS 导航，除了 DWA 和 TEB 还有没有其他选择？》](https://www.bilibili.com/video/BV1nQR4YsESM/)

## 下载源代码

1. 获取源码:
```
cd ~/catkin_ws/src/
git clone https://github.com/6-robot/jie_ware.git
```
国内镜像：
```
cd ~/catkin_ws/src/
git clone https://gitee.com/s-robot/jie_ware.git
```
2. 编译
```
cd ~/catkin_ws
catkin_make
```
## 激光定位
1. 修改导航Launch文件，用如下内容替换AMCL节点：
```
<node pkg="jie_ware" type="lidar_loc" name="lidar_loc" >
    <param name="base_frame" value="base_footprint" />
    <param name="odom_frame" value="odom" />
    <param name="laser_frame" value="laser" />
    <param name="laser_topic" value="scan" />
</node>
```
2. 运行修改后的Launch文件
```
roslaunch jie_ware lidar_loc.launch 
```
## 代价地图清除
1. 修改导航Launch文件，添加如下内容：
```
<node pkg="jie_ware" type="costmap_cleaner" name="costmap_cleaner" />
```
2. 运行修改后的Launch文件，正常设置机器人的估计位置即可。
## 激光雷达滤波
1. 修改导航Launch文件，添加如下内容：
```
<node pkg="jie_ware" type="lidar_filter_node" name="lidar_filter_node" />
```
2. 修改代价地图参数文件 costmap_common_params.yaml ，将激光雷达数据话题 topic 从 scan 修改为 scan_filtered 。
```
  observation_sources: scan
  
  scan:
    data_type: LaserScan
    topic: scan_filtered
```
3. 运行修改后的Launch文件，正常进行导航。

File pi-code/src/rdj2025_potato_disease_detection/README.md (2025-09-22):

# rdj2025_potato_disease_detection

A ROS 2 Humble package for **potato disease detection** using a machine learning model.  
The package subscribes to an image topic (`/image`), runs inference, and publishes results to `/inference_result` and '/inference_image'

## 📦 Package Overview

This package contains:

- **`potato_disease_detection_node`**  
  - Subscribes to `/image` (`sensor_msgs/Image`)  
  - Converts the image into OpenCV format (via `cv_bridge`)  
  - Runs inference using a provided ML model (you can replace with your own)
  - Publishes results on `/inference_result` (`std_msgs/String`)
  - Publishes results on `/inference_image` (`sensor_msgs/String`)

- **`test_image_publisher`**  
  - Publishes a static test image (`potato.jpg` or another local image)  
  - Sends it to `/image` for testing the detection node
    
- **`rtsp_image_publisher`** 
  - Connects to an RTSP stream from the Raspberry Pi camera  
  - Displays a live preview in an OpenCV window  
  - On pressing **`d`**, saves the current frame to a configurable directory and publishes it to `/image`  
  - On pressing **`q`**, exits cleanly  
  - Accepts the Pi’s IP address as a ROS 2 parameter (`pi_ip`)

## Dependencies

⚠️ Note: `cv_bridge` currently only supports **NumPy < 2.0**.  
If you see `_ARRAY_API not found` errors, downgrade NumPy:

```bash
pip install "numpy<2" --force-reinstall
```

Also, install PyTorch (Used for Inference)

```bash
pip3 install torch torchvision --index-url https://download.pytorch.org/whl/cpu
```

## Build Instructions

# Go back to root (parent) workspace directory
cd ~/your_root_directory

colcon build
source install/setup.bash
```

## Running the Nodes

### 1. Run the Inference Node

```bash
ros2 run rdj2025_potato_disease_detection potato_disease_detection_node
```

This will start the potato disease detection node. It will wait for images on `/image`.
On receiving an image it will run an inference displaying a text on the terminal. 
An annotated image will also be published to the '/inference_image' topic which can be view in RVIZ2 under the 'Image' display plugin

### 2. To start the feed stream from raspberry PiCamera2
open a script and run the following script: 

```bash
rpicam-vid -t 0 --nopreview --inline --codec mjpeg \
  --width 1280 --height 720 --framerate 15 \
  --hflip --vflip \
  -o - | ffmpeg -f mjpeg -i - -c:v copy \
  -f rtsp -rtsp_flags listen rtsp://0.0.0.0:8554/cam
```

### 3. Publish a Test Image

In a new terminal (with workspace sourced):

```bash
 ros2 run rdj2025_potato_disease_detection publish_test_image  --ros-args -p pi_ip:=<your_pi_ip>

```

This will publish `xxxxxx.jpg` (make sure the file exists in the working directory).  
It will also automatically publish an image on the '/Image' topic every time 'd' is pressed.

### 3. Inspect the Inference Results

Use another terminal to view the published inference results:

```bash
ros2 topic echo /inference_result
```

##  Visualizing Images

You can view the published images with:

```bash
ros2 run rqt_image_view rqt_image_view
```

## Next Steps

-   Deploy on a robot with a camera publishing to `/image`.

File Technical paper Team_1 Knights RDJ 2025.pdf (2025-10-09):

[Team 1] | 1 of 11

# Technical Design Paper Template for the Robotics Dojo Competition 2025

First A. Amos Oniare, Second B. Dismas Karimi, Third C. Gareth Kipkoech, and Fourth D. Fundi Brian (KNIGHTS)

I. INTRODUCTION
Robotics Dojo is a project-based robotics training program under the AFRICA-ai-JAPAN Project at the Jomo Kenyatta University of Agriculture and Technology with its primary objective being the encouragement of robotics research in Kenya. The program creates a robotics challenge each year in which students form teams and compete. The challenges are always evolving from previous years in an effort to build robots that can be beneficial in the real world environments such as industries.
This year’s challenge was the design and development of an autonomous mobile robot that can collect and offload loads while navigating on uneven terrain, within a changing environment and use a camera for image detection and classification of potato diseases. The robot’s performance is gauged on how accurately and fast it can perform navigation, image detection and collection and offloading of loads. This is an improvement of last year’s challenge that only included autonomous navigation of a mobile robot.

II. DESIGN STRATEGY The robot had to be able to do the following: ● Map of its environment and save the map. ● Autonomous navigation of its environment using the saved map. ● On board load transportation and dropping at a designated location. ● Image classification of healthy and diseased potatoes using a camera.

The above requirements were met by use of appropriate mechanical, electrical and software systems that worked together to accomplish a common goal. After careful consideration, the following elements that make up the robot were created:
| ● Robot frame ● Offloading mechanism ● Drivetrain and propulsion ● Power Supply ● Wheel mounts and wheels ● Control Scheme ● Environment detection devices ● Mapping, Localization and Navigation system ● Image detection system

Robot Frame

It represents the physical structure that supports all the components such as sensors, actuators, electronics and other mechanical elements of the robot. It was made from acrylic which is relatively simple to fabricate using a laser cutter and offers sufficient mechanical strength ensuring the robot has a rigid core that can sustain collisions without damage and can reduce vibration transmission that may influence the accuracy of sensor data.

Of loading mechanism

An arrangement was devised that could tilt the bed as well as open the gate using only one actuated link.The arrangement consisted of a bed-tilting mechanism and a gate actuation mechanism.

The bed tilting mechanism was a four-bar chain in double-rocker configuration. It is illustrated in figure A. The bed was the follower link, a servo arm being the crank and a coupler connecting rod.

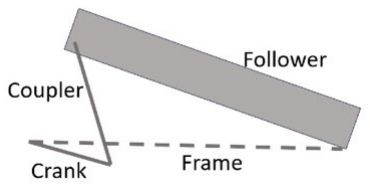
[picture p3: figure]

Figure A: Bed tilting mechanism

The gate forms part of a simple first class lever anchored on one side by a hinged link. It is illustrated in figure B. The pivot link and gate were rigidly connected, making them a single link.

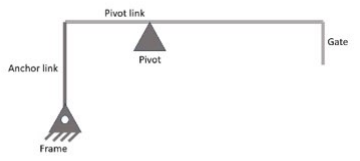
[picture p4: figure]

[Team 1] | 2 of 11

Figure B: Gate actuation mechanism

With this arrangement, it was possible to pivot the bed as well as raise the gate using only one actuated link.

Drivetrain and propulsion

This system was required to move the robot accurately and reliably on uneven terrain. It was made up of 4 motors with rotary encoders to provide odometry data and was powered by a lithium polymer (LiPo) battery via the drv8833 motor drivers. The number of motors was chosen to be four to increase traction in unstable surfaces and increase total propulsion power in moving the robot on inclined planes.

Wheel mounts and wheels.

The wheels chosen were of 85mm in diameter and with spikes for a firm grip to the ground. The wheels had a thickness of 36mm allowing bigger ground coverage for robot stability. These wheels were rotated using four motors which had maximum revolutions per minute (RPM) of 200. Hexagonal couplings were used to attach the wheels to the motors. The wheels-motors assembly was then mounted to the chassis of the robot using mounting brackets.

Control Scheme

This section was divided between the Mobile platform and navigation system of the robot. An STM32F4 microcontroller was used for the mobile platform because of its adequate input and output pins and relatively more interrupt pins compared to arduino mega. It was responsible for sending commands to the motors, reading encoder and IMU data and using a serial connection to send the data to the navigation system for processing.

The navigation system required a processor capable of hosting the Robot Operating System (ROS2) and the Raspberry Pi 4 was chosen because of its sufficient processing speed and relatively low power requirements. Its function was to receive data from the STM32F4 and Lidar, process them and send appropriate motor commands to the STM32F4.

Environment detection devices

The sensors used for the robot setup were quadrature encoders, MPU-6050, RPLIDAR A1 M8 and the PiCamera module 2. The encoders were used to track wheel rotation. This information would assist the robot to calculate its estimated position and trajectory. The MPU-6050 was used to measure the robot’s orientation and movement by integrating a gyroscope and an accelerometer. To mitigate the odometry drift the encoder data and inertial measurement unit (IMU) data were combined using sensor fusion. The LIDAR was used to detect objects within the environment of the robot using an infrared (IR) laser scan.

This data was used for simultaneous localization and mapping (SLAM) of the robot as well as during navigation to allow the robot to detect the introduction of new obstacles into its environment. The PiCamera was used to capture images of plant leaves displayed on a screen for classification using a machine learning model. The possible categories were “healthy”, “early blight” and “late blight”. The PiCamera color detection on an LED strip mounted in the game field for distinguishing payloads.

Power Supply

A Lithium Polymer battery was chosen to power the Mobile platform due to its high energy density and relatively light weight. The relevant power requirements for each electrical device were calculated and used in determining the appropriate charge capacity of the battery. Switches were also used to disconnect the power source from the electronic components when the robot was not in use to reduce the likelihood of accidents caused by short circuits occurring. The navigation system was powered by an 18 W power bank that was connected to the Raspberry Pi which then powers the lidar.

Mapping, Localization and Navigation System
- Mapping [1]. This was possible by using the laser scan from the LIDAR to visualize the robot’s environment. This was carried out using the slam toolbox and a file containing the mapping parameters such as scanning range, resolution, maximum loop distance among others needed to generate a clear map that the robot can later refer to. It was possible to create a good map because of utilizing the Extended Kalman Filter (EKF) sensor fusion algorithm to combine the IMU data with encoder data for accurate and reliable estimate of the robot’s position and velocity. Therefore, even if the actual robot skidded then in RVIZ2, the skidding would not be registered as a robot’s movement. The map was visualized in RVIZ2 and later, if satisfied with its clarity, saved and serialized for use in localization.
- Localization. For the robot to understand its location with reference to its surroundings then the saved map was used by loading it as a parameter during localization. Upon starting the localization launch file, the earlier created map would be loaded on to RVIZ2 and if not satisfied with the robot’s analysis of its current location, then a pose estimate would be provided.
- Navigation. After localization, the robot was now ready to autonomously navigate through set way points or to just one set goal. With the assistance of the nav2 stack with tuned parameters different from the default, the local and global costmaps showed the robot’s weight allocation to different obstacles in the environment and thus being able to

[Team 1] | 3 of 11

find an obstacle free path however long or short. A
notable implementation is adoption of the Model
Predictive Path Integral (MPPI) controller instead of the default Dynamic Window Approach (DWA) critic based controller after the former outshined the latter in multiple simulation runs.

The general steps taken in the design and development of the robot were as follows:
- A model and design of the robot frame and loading and offloading system was created using a CAD (Computer Aided Drawing) software while ensuring the robot dimensions were within the allowed limits i.e, 300 x 300 x 200 mm.
- Acrylic was chosen as the fabrication material and a laser cutter was used to cut the desired shapes making up the robot structure.
- The robot chassis was assembled using appropriate screws and hot glue where necessary.
- A Bill Of Materials (BOM) was created for purchasing electrical components and other consumables.
- An electrical circuit was designed and transferred onto a perforated board by soldering the electrical devices and connection header pins in place.
- The electrical and electromechanical components were connected to the circuit.
- Testing was done on the Mobile platform to ensure it was following instructions from a written algorithm.
- The sensing elements were added to the circuit and the Raspberry pi, connected to the lidar, was connected via serial to the STM32F4.
- Image | detection | and | classification | was
implemented using the Raspberry Pi Camera module 2.
- Image data was used to coordinate the loading and offloading process.
- Mapping and Navigation was then developed, tested and improved.

III. VEHICLE DESIGN
This section discusses the design process in detail and explains the methodologies used during the fabrication, assembly and programming of the robot. The vehicle design was split in three: the mobile platform design, navigation system design and the computer vision system design. Improvements from last year’s robot design was also noted and discussed.
1. Mobile Platform
This consists of the drivetrain and the loading and offloading system. Figure 1 shows the robot design that was created.
The 2D dimensioned views of the robot’s frame are shown in Figure 1.

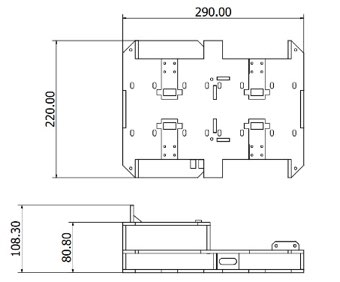
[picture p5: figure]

Figure 1: 2D dimensioned robot frame
The 2D dimensioned views of the motor holder and coupling assembly is shown in Figure 2.

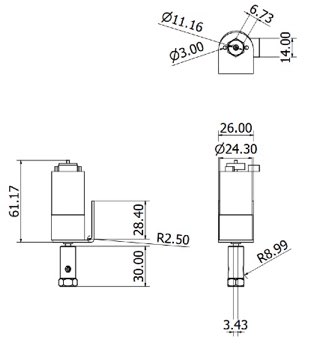
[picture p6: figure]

Figure 2: 2D dimensioned motor-coupler assembly

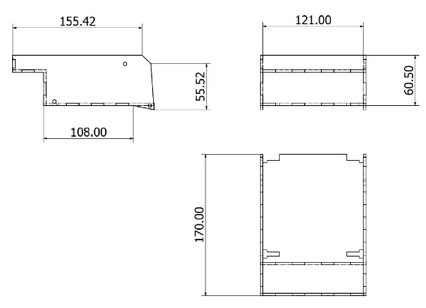
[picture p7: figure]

Figure 3: 2D dimensioned courier/bed

[Team 1] | 4 of 11

The 2D dimensioned views of the robot’s bed used as
courier for the colored cubes are shown in Figure 3.
A tagged 3D robot model is shown in Figure 4. It gives an overview of the outlook of the designed robot in Autodesk Inventor.

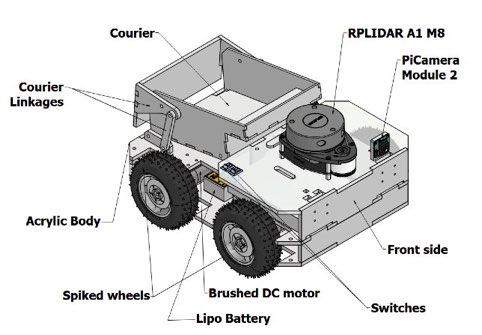
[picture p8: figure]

Figure 4: Tagged 3D robot model

The robot consists of 2 acrylic layers at its base, 3 layers for its front half and a loading and offloading mechanism at its rear half. Acrylic was chosen as the fabrication material because of the following:
- High impact resistance which is 10 times higher than glass.
- It is Lightweight.
- It has excellent dimensional stability.
- Innate weatherability and UV resistance.
- High optical clarity. (Makes it easier to identify problems in electrical connections within the body)
- Requires less energy when laser cutting as compared to other materials like aluminum.
- Its lower price compared to other durable alternatives like metals.
Laser cutting was chosen as the preferred method of manufacturing instead of other methods such as 3D printing because of the following advantages:
- Low lead time in fabrication
- High precision geometries and low tolerances. The robot was designed to have a low height and to accommodate the heavy components in the lowest layer, with the aim of minimizing the height of the centre of mass. Four motor driven wheels were chosen to allow the robot to have greater maneuverability and propulsion on uneven and unstable surfaces such as gravel and woodchips. The downside of using four wheels is that extra developments were needed to account for drift of the robot’s odometry during turning on the spot using a differential drive system. This error necessitated incorporation of an IMU and correction algorithms. The implementation of this correction system is discussed in depth in the navigation system.
Once the robot frame design was completed, its electrical system was tackled, involving proper component selection and integration. Power calculations were performed for power supply sizing. The motor selection was informed by target robot acceleration.
The final robot was estimated to weigh approximately 4kg. A target maximum acceleration of 0. 5m/s was

2
selected. Given the above two considerations and assuming a worst case 50% efficiency, the required motor torque is given by:
T = | , where a is the

a×m×r
N×η =

0.5×4×0.0425
4×0.5 = 0. 0425 Nm
target acceleration, m mass of the robot, r radius of the drive wheels and N the count of driven wheels
A target speed of 0. 8m/s is selected. Given the wheel radius, the appropriate motor rotation count is given by:
RPM = | , where v is

60v
2×π×r =

60×0.8
2×π×0.0425 = 179. 751rpm
the target speed, and r is the driven wheel radius.

Typical current draw is calculated with the relation:
I = | , where T is

T×ω
V =

0.0425×2π×179.751÷60
10.5 | = 0. 0762A
the required torque, ω is the required angular velocity and V is the supply voltage.
The motors best matching the requirements above are found to be 12V, 200rpm with encoders.
The other components that make up the mobile platform include:
- DRV8833 - A Dual H-Bridge Motor Driver with 1.5 A peak current output per channel and under-voltage, over-current, and over-temperature protection.
- Hex Coupling - Used for connecting the motor shaft to the wheels.
- STM32F4 microcontroller - Used for low-level tasks like controlling motors, fetching data from encoders and IMU.
- 4 brushed DC motors with quadrature encoders-For propulsion.
- MG996R Servo Motor - Used for loading bed actuation.
- Lipo battery - Providing electrical power to the system.
- Perforated board - For mounting and soldering electronic components.
- Power Switch - Allows for the isolation of the electrical circuit from the power source when the robot is not in use.
- Buck converter - Steps down DC voltage from battery.
- Japan Solderless Terminals (JST) - Used for component connection to the main board.
- Male and female header rows - Used for modules and cable connection.
- Cable ties - For bundling and securing wires and electronics.
- Motor mounting brackets - For securing the motors to the robot frame

[Team 1] | 5 of 11

Once the components were selected and a circuit made,
power calculations were applied to determine the correct rating of the Lipo battery and verify if the connections were safe and functional.
P = IV (Watts) | equation ‘I’
Where; ‘P’ is Power in Watts
‘I’ is Current in Amperes
‘V’ is Voltage in Volts
The following chart is the representation of the electrical circuit with the current and voltage values of each component. Devices operating on the same voltage value were connected on the same voltage line and their current draws were summed as shown in Figure 5.

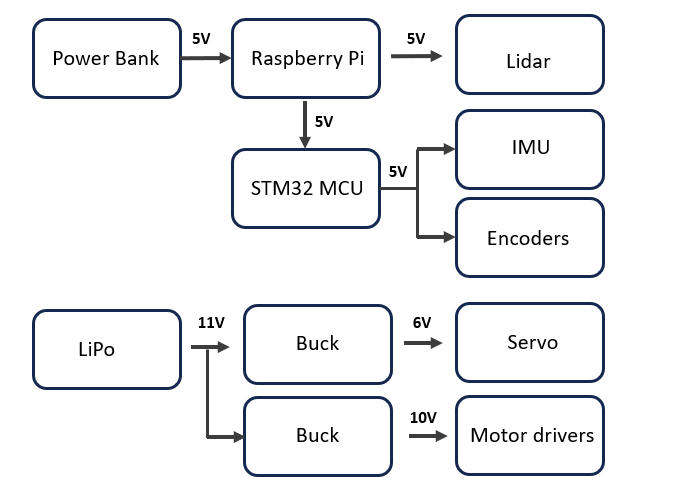
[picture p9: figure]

Figure 5: Electrical flow diagram
Two power sources were used, one for powering the Raspberry Pi and the other the motors. It was more convenient to use a power bank with a type C cable to power the raspberry pi. To determine if the Power Bank was capable of providing enough power, the total power drawn by the Raspberry Pi and the RPLidar was calculated as follows:
P = (1.5 x 5) + (1 x 5)= 12.5W
This value is well below the rated value of the power bank. The capacity of the power source for the rest of the components was determined by calculating the power requirements of each device and finding their sum.
Power from Lipo ≈ Peak power required by (1 Servo motor and 4 DC motors and encoders)
P ≈ (2.5 x 6) + 4(1.5 x 10) = 75 W
Therefore the 3S 2200mAh Lipo battery that was chosen had a Power rating of 24.4 Wh which can supply the peak current required by the system at 11 V.
Closed loop control of the motors was achieved by implementing the PID (Proportional Integral Derivative) control which is made up of the following elements:
- Proportional (P) Coefficient Kp - Its effect increases proportionally with magnitude of error. It increases responsiveness of the system but cannot effectively eliminate steady-state error. It was decided after testing to assign it a value of 200.
- Integral (I) Coefficient Ki - Its effect grows as the sum of errors over time increases. It therefore controls steady-state error. It was assigned a small value of 1, as much larger values increase system instability.
- Derivative (D) Coefficient Kd- Its effect increases when rate of change of error increases. It therefore controls overshoot by slowing down change as the final value is approached This coefficient was set to the value 120.
- Scale Ko - It scales the output of the controller by a factor. The value found appropriate was 50.

Challenges in Hardware Implementation
1. USB device enumeration failure - attempts to program the microcontroller over USB were initially unsuccessful. The STM32F4 would not be recognized as a USB device by the computer, regardless of the Operating System used. It was discovered that some Input-Output (IO) pins are inappropriate for use with the USB bootloader. The USB FS D+ and USB FS D- pins in particular had the greatest effect. Figure (i) shows the STM32F401 pinout and the affected pins.

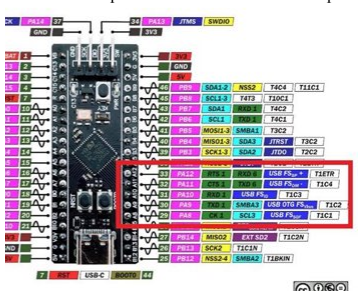
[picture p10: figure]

Figure (i): STM32F401 pinout with affected pins highlighted
The solution was to move IO devices from those pins to unaffected pins.
2. Motor jerk when running closed loop motor control - open loop motor control performed as expected, and reading encoder data alone by spinning the motors by hand was okay as well. However, activating both motors and encoder reading produced erratic behaviour. After extensive research and testing, it was discovered that motor wire length and shape was the contributor. To keep wiring tidy, excess motor and encoder cables had been coiled into loops. This unintentionally created strong electromagnetic coupling between the noisy motor power lines and the sensitive encoder signals. The result was EMI from inductive, capacitive, and antenna-like

[Team 1] | 6 of 11

effects, which corrupted encoder readings. As a
workaround, motors had to be driven at a low
PWM frequency of 500 Hz and lower. The figures (ii) and (iii) illustrate the cable management.

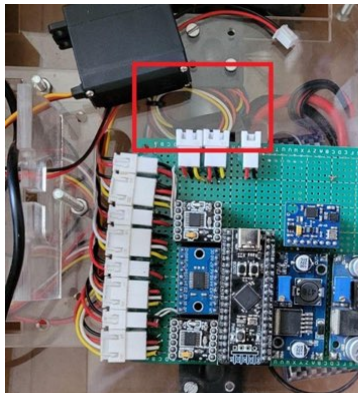
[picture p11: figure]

Figure (i): Wire loops present before.

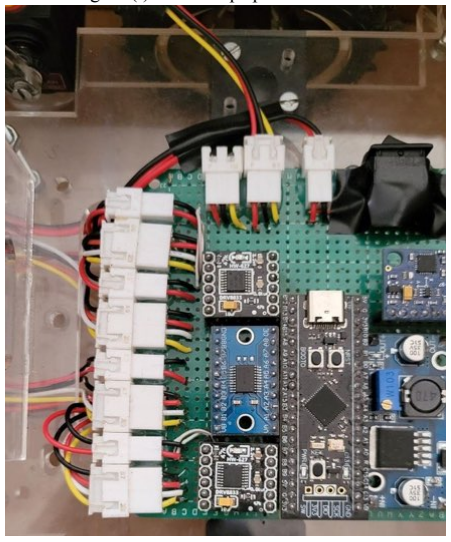
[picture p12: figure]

Figure (ii) Wire loops removed.

After removing the loops and shortening the cables, the interference was eliminated, and clean encoder signals were maintained even with PWM frequencies above 30 kHz.

### 2. Navigation System

In the design of the robot navigation system, multiple critical steps were covered, including data conversion from encoders and IMU, SLAM mapping, and path planning. A comprehensive robot navigation system framework to realize the navigation capability was designed. This
framework | implemented | distributed communication
through the ROS system, enabling collaboration between SLAM mapping and navigation path planning. A high-level overview of the system is shown in Figure 6.

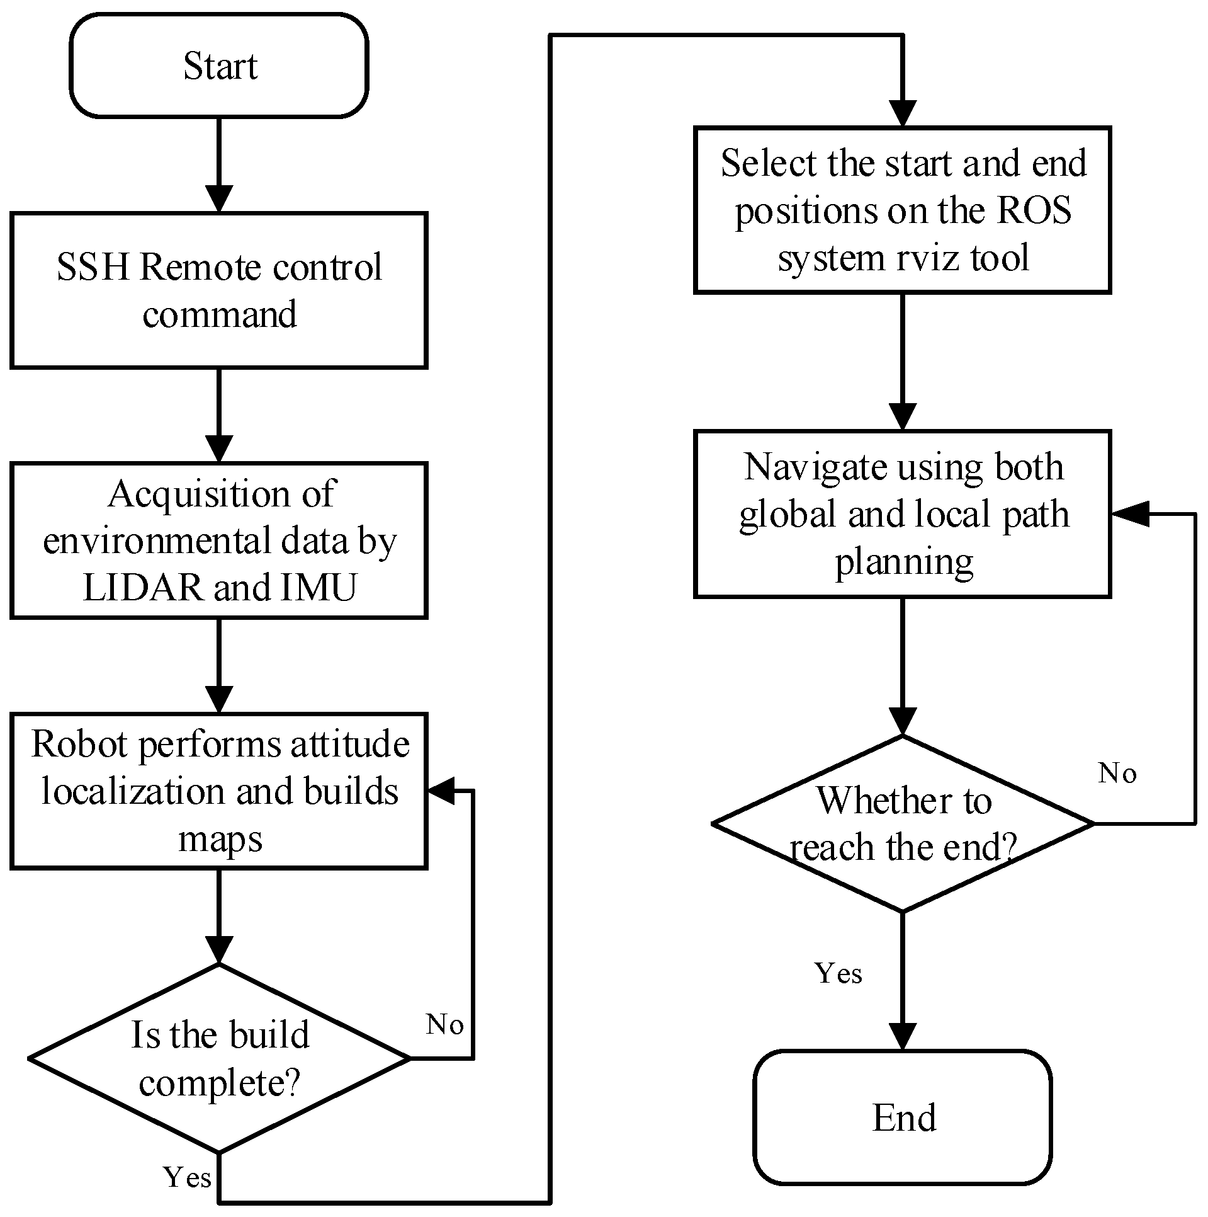
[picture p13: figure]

Figure 6: Navigation System Flow Chart

In the previous Robotics Dojo competition, encoder data was the only source of odometry data for the robot. The position of the robot was calculated based on counts of wheel rotations and the differential robot motion model. This is a simple method for robot localization but it only works accurately when the robot’s wheels do not slip. This year’s competition features uneven terrain and loose surfaces making it increasingly difficult to achieve motion without any slip, which throws off the localization. To solve this problem, an Inertial Measurement Unit (IMU) was introduced to complement the encoders. Data from both streams was used together to provide accurate and reliable robot localization even with wheel slip. This method of using data from more than one sensor for a single purpose is known as sensor fusion and it has the following advantages:
- Enhances accuracy of resultant data.
- Increases robustness of the system as it will continue functioning even if one sensor fails.
- Provides resilience against intermittent/missing data
The Extended Kalman Filter (EKF)[2] was used to make the system resilient to sensor noise for steady more meaningful readings. EKF is a development on the Kalman Filter which allows it to process non-linear functions of a system, better suited for real world applications. The basic principle of operation of this filter is as illustrated in figure 7:

[Team 1] | 7 of 11

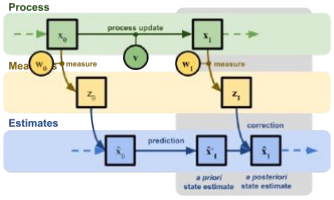
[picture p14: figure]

Figure 7: Extended Kalman Filter Illustration
The process represents the system being monitored such as a moving body, the measurements stand for the data collected from sensors and estimates are the results from the filter’s model of the system. From a high-level perspective, the algorithm follows a 2-step cycle: (1) Predict, (2) Update.
In the prediction step, the system’s state is projected forward using a non-linear motion model, creating the priori state estimate. In the update step, incoming sensor measurements are compared to the predicted state, and the state estimate is corrected to create the posteriori state estimate.
Using the XYZ coordinate frame with Z pointing up from the floor, the robot’s state (position and orientation) can be described by just 3 values: X position, Y position and Yaw angle (rotation angle about the Z axis).

The state estimate is a function of the previous state, the previous velocities and some noise term. Mathematically stated[3]:

state

t = state

t−1 + dt × velocities

t−1 + noise
In matrix form, and substituting the differential drive model we get:

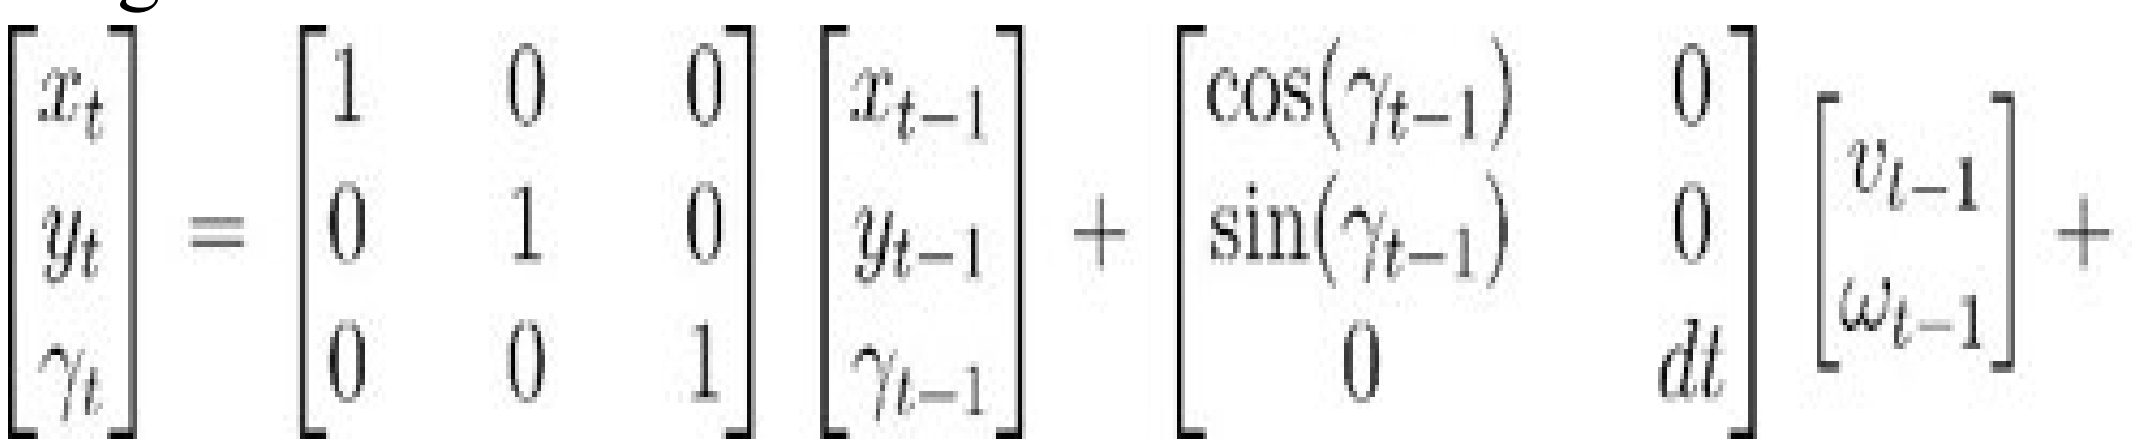
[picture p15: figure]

state provides the current state estimate.
t
Now the predicted sensor measurements is given by[3]:

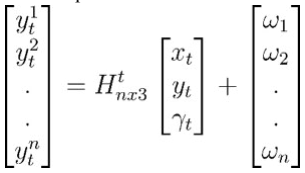
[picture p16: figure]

Where H is the measurement matrix, n is the number of sensor measurements at time t, and is the sensor noise term.
Once the estimated state and predicted sensor measurements at current time t are obtained, a weighted average is calculated to create an improved current state estimate. The successive steps in the EKF algorithm automatically determine the appropriate weights. Robot_localization[4] a ROS2 package makes implementation of EKF in a project simple. The required inputs are the wheel encoder data, the IMU data, process noise covariances and velocity commands. The filter is applied to all sensor inputs before being combined to obtain a single reliable odometry output. The computation is done by a node named /ekf_node, which is subscribed to the /imu/data and the /diff_cont/odom topics. The node then publishes processed odometry data to the /odometry/filtered and /tf topics. The former is the current state estimate of the robot and the latter is the current transform of the robot base link.
Other than noise reduction, the EKF robustness against gaps in data collection due to, say, sensor interruption. This is because the prediction step, which utilizes the differential drive robot model, can extrapolate into the future. However, prediction for extensive durations leads to error accumulation, since sensor data, although noisy, still contains some information. This information is crucial for correction where predicted data is compared with noisy data to obtain a final state estimate that is both accurate and low in noise.

Robot navigation was achieved using the ROS2 Nav2 stack for path planning and control while slam toolbox was employed for SLAM.

### 3. Computer Vision System

This section was implemented using the Raspberry Pi Camera Module 2 which was the image source. The image data collected had the following functions:
- Classification of potato leaves as being healthy, having early blight or late blight.
- Coordinated the loading and offloading process Classification of potato leaves was achieved using a package provided by Robotics Dojo with a trained model. The package creates a node subscribed to the /image topic and an inference engine whose result is annotated onto the source image. The labelled image is then published to the /inference_image topic which can be visualized in RVIZ under the Image display plugin.
The goal for Robotics Dojo was to make loading and offloading processes fully automated. The robot would have to discriminate loads based on color and deliver the load to a bay of matching color. During loading, two LED strips were placed in front of the loading bay to give a signal on the color of the load the robot has received such as lighting the red led strip when the load is of a red color. The robot then identifies and saves the led color, proceeds to navigate autonomously to the offloading bay and once again uses the camera to identify the bay with a matching color as the load it is carrying such as offload on the red bay if the load carried is red.
A simple workflow was implemented using the OpenCV[5] module in Python. OpenCV allows detection of

[Team 1] | 8 of 11

entities in an image such as color, shapes, faces and many
more. The camera was run continuously to fetch real-time
images. Using the Real-Time Streaming Protocol (RTSP), the images were sent over IP from the Raspberry Pi to the main computer for processing. This was adopted to relieve the raspberry pi off the heavy inference processing duties. The algorithm running on the main computer for simple real-time color detection was as follows:
1. An image is fetched from the RTSP stream and saved to memory
2. The image is converted from BGR to HSV color spaces
3. Color ranges in HSV format are defined
4. Using the color ranges, a mask is created for each color
5. The mask is dilated (a morphological transform) to reduce effects of image noise
6. Contours in the masked image are identified
7. Bounding rectangles corresponding to the contours are drawn on the image for tracking
8. Bounding rectangles are counted
9. Text is affixed for each bounding rectangle
10. The color with the largest count of bounding rectangles is published to a ROS topic /detected_color
Simple conditional checks were created to check for specific sequences in detected color. Servo actuation would be done only if a color was detected for 2 consecutive detection events after a time interval.
Challenges in Implementing Color Detection
An initial implementation of the algorithm had step 8 identify the largest contour by area. While initially promising it failed when the target color did not cover the full Field-of-View of the camera. The simple algorithm would, for instance, identify the color of the frame of the screen as well as the color shown on the screen itself. Of course this gave erroneous results that broke the algorithm downstream. However, it was noticed that for a given target color, many contours would be identified within the frame, along with one large contour for the frame on the screen. The team decided to shift strategy to counting bounding boxes, rather than ranking them based on area.

IV. EXPERIMENTAL RESULTS
The performance of the robot was tested and assessed in the following areas:
- Quality of map produced.
- Accuracy of colour detection.
- Coordination of the courier offloading based on image data.
The quality of the map produced was greatly dependent on the source of odometry data. A comparison was made on the maps obtained by using encoder data only and when using sensor fusion to combine encoder and IMU data. Two simple tests were done in simulation:
1. Turning in place 90 degrees clockwise from the initial position
2. Driving around a complete loop from the initial position

Figures 8 and 9 show the initial position of the robot at
launch | of | SLAM | .

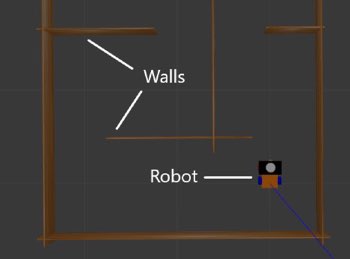
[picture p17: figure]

Figure 8: Virtual robot initial position

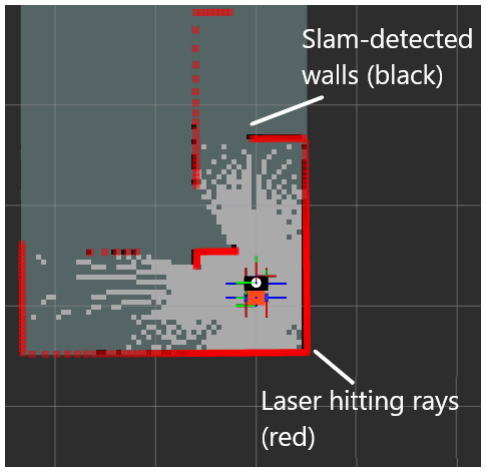
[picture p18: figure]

Figure 9: Rviz visualization at initial position

Figure 10 shows the result of turning in place without fused odometry.

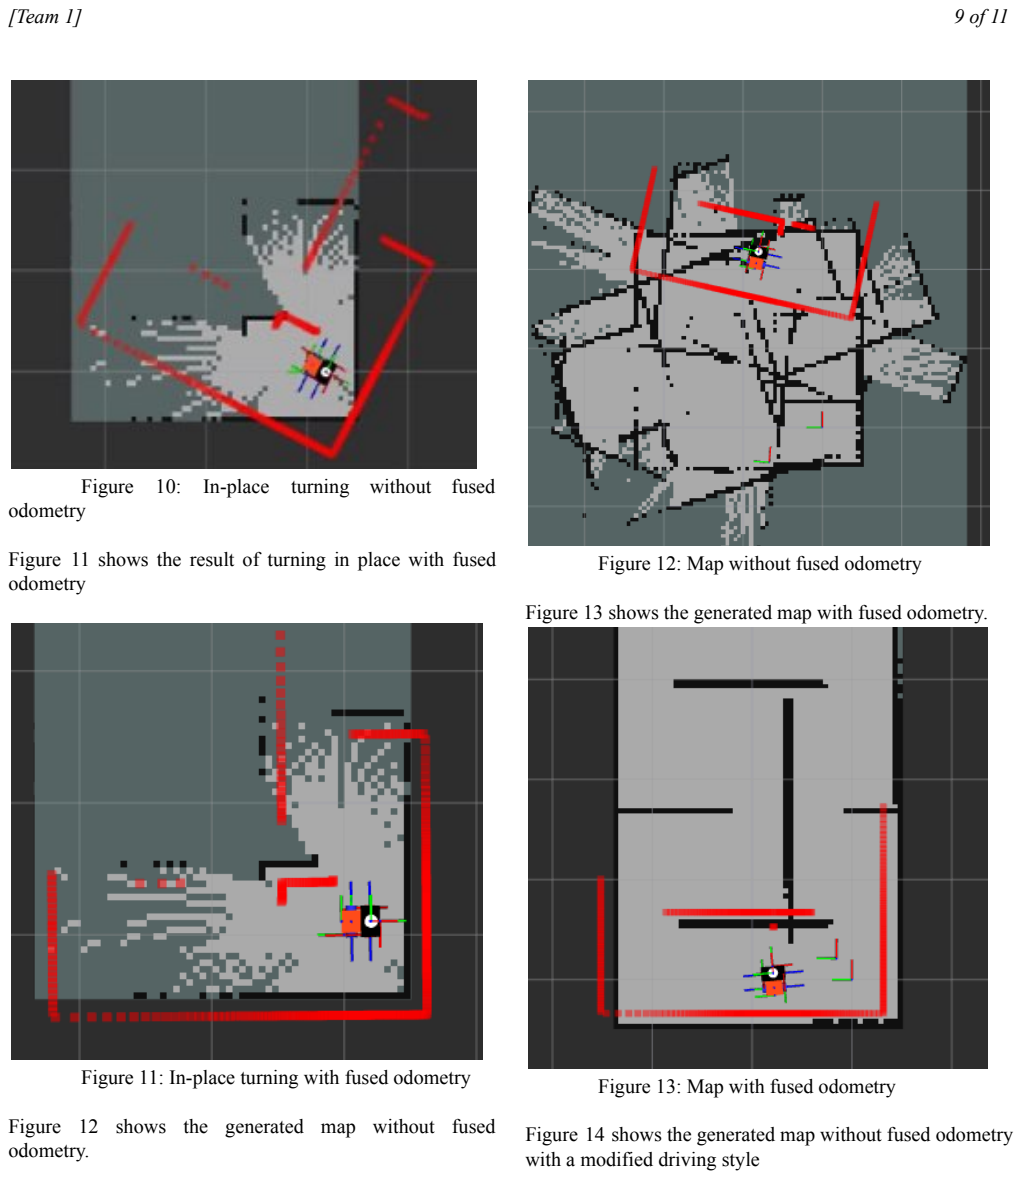
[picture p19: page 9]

[Team 1] | 9 of 11

Figure 10: In-place turning without fused odometry

Figure 11 shows the result of turning in place with fused odometry

Figure 11: In-place turning with fused odometry

Figure 12 shows the generated map without fused odometry.

Figure 12: Map without fused odometry

Figure 13 shows the generated map with fused odometry.

Figure 13: Map with fused odometry

Figure 14 shows the generated map without fused odometry with a modified driving style

[Team 1] | 10 of 11

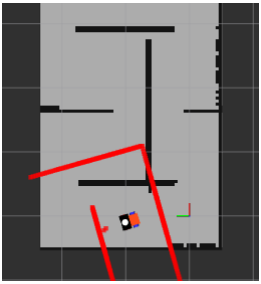
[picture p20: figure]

Figure 14: Map without fused odometry with modified driving style

It is quite clear from figures 10 and 11 that sensor fusion performs considerably better than odometry with wheel encoders alone. There still exists some translational drift in laser scan in figure 11 however in practice this is easier to compensate for than rotational drift. Figures 12 and 13 illustrate that EKF is indispensable as the map without fused odometry is unusable, and further cement the difference in significance between translational and rotational drift. An interesting finding shown in figure 14 was that the driving style also played a role. To obtain that result, in-place turning was avoided completely, instead opting to combine some linear velocity with all angular velocity. However, the alignment of the laser frame was still compromised at the tail end of the run when restoring the robot’s orientation. This proves that although it is possible to map accurately without IMU data, it is not dependable, especially since autonomous robot navigation extensively uses in-place turning to clear up laser scan drift.

The results from the real robot closely resembled those obtained from simulation.

The Courier was designed to offload only when the robot had arrived at the offloading bay that was colored to match the color of the object loaded on the robot. OpenCV was used as a tool to classify image data into a specific range of colors such as red or blue. Additional functionality was added to this image controlled loading and offloading process to ensure that it functions as designed. OpenCV allows one to write a python script that displays an image from the pi camera with labelled rectangular contours encircling an identified image such as a color or an object.

Two methods of color identification were implemented and compared. The first was selecting the largest contour by area and publishing the identified color as the label of the contour and the second was selecting the label with the most contours and publishing the label as the identified color. The described methods are illustrated in the following image:

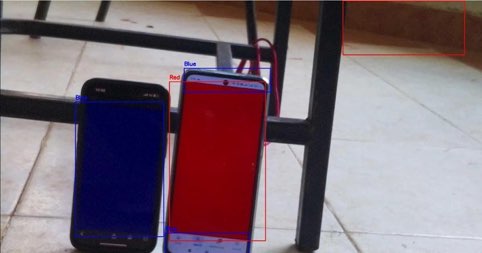
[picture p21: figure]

From the image, it is observed that the red contours are two in number while the blue contours are three in number while the largest contour by area is the red contour, only if the larger red contour in the background is ignored.
As discussed in the Vehicle Design section, the latter method was chosen because of the following reasons:
- It was less prone to error. The first method could identify a contour larger than the object being observed in the background and send the wrong data. The second method would rely on contour concentration, such as an led, and send the led color as the correct color of the image.
- It was more reliable. An object with a consistent and bright color will trigger the correct color
identification | without | being | affected | by
background color identifications that may not have high intensity.
V. ACKNOWLEDGEMENT
The Robotics dojo competition development and implementation was greatly dependent on the 2025 Robotics dojo interns who created comprehensive video and written tutorials, as well as presentations on various topics. Acquisition of robotic parts was also made possible by the Japan International Cooperation Agency (JICA).

VI. REFERENCES
[1] E. Renard, ROS 2 from Scratch: Get Started with ROS 2 and Create Robotics Applications with Python and C++.* Birmingham, U.K.: Packt Publishing, 2024, pp. 343–344.
[2] Ribeiro, M. I. I. (2004). Kalman and extended Kalman filters: Concept, derivation and properties. Institute for Systems and Robotics, 43(46), 3736-3741.
[3] AutomaticAdisson, Extended Kalman Filter with
Python, | 2025, | Online
https://automaticaddison.com/extended-kalman-filter-ekf-w

[Team 1] | 11 of 11

ith-python-code-example/.
[4] Tom Moore, Robot Localization Wiki, Online Article,
2024,
https://docs.ros.org/en/melodic/api/robot_localization/html/i ndex.html
[5] Raguraman, P., Meghana, A., Navya, Y., Karishma, S. K., & Iswarya, S. (2021). Color detection of RGB images using Python and OpenCv. International Journal of Scientific Research in Computer Science, Engineering and Information Technology, 7(1), 109-112.

VII. APPENDIX–SITUATIONAL AWARENESS
A significant challenge in adoption of unmanned systems is user trust. Many applications to which robots may be of great benefit remain unautomated simply because of lack of trust. This highlights the need for communication between the designer and the ultimate consumer of the system. Therefore to bridge that gap, this team would do the following:
| ● Inform the user that the system is autonomous,

what autonomy means and what they should expect.
- Explain the most relevant constituents of the system, especially components visible to the user.
- Communicate what the robot is designed to do, and what role the user plays in its successful operation.
- Discuss common misconceptions and Frequently Asked Questions about what the robot can and can’t do.
- Cite internal and/or external testing and validation data that shows the product can complete the task, also listing confidence levels and uncertainties.
- List fault conditions, how to identify them, and resolve them if possible.
- Communicate that corner cases do exist and may not be accounted for.
- Emphasize that the robot is not sentient or innately malicious.

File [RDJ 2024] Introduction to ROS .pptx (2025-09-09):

## Introduction to the Robot Operating System (ROS)

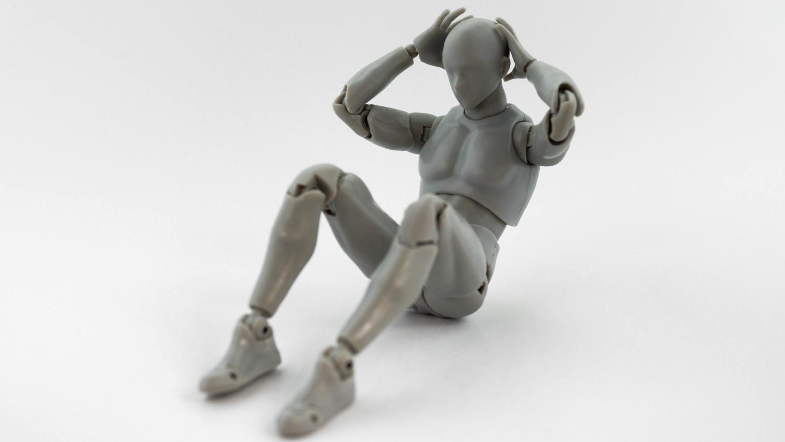
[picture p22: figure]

## Lenny Ng’ang’a

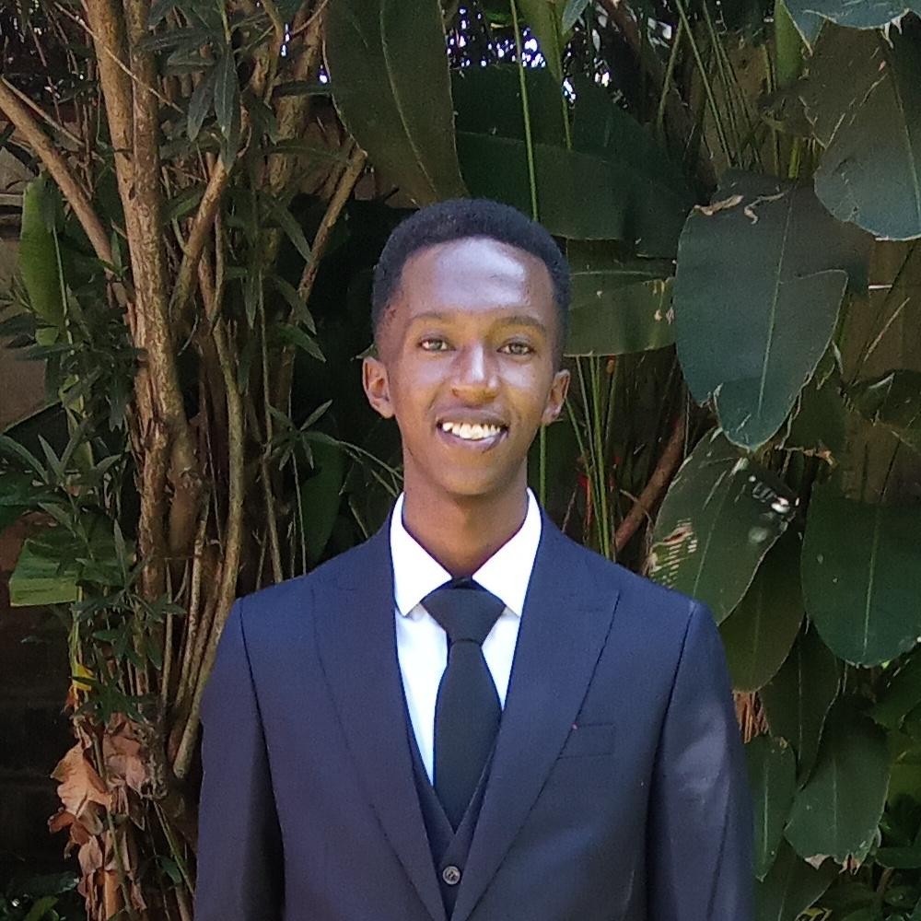
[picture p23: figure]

- Robotics Dojo 2022 & 2023
- Robotics Dojo Trainer 2023
- Robotics Dojo Research 2024

## Robot Operating System

- The Robotics SDK
- Not an Operating System
- Middle-ware

## Why ROS?

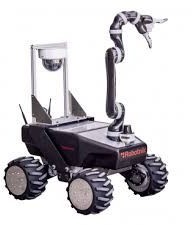
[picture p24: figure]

- Distributed Computing

## Why ROS?

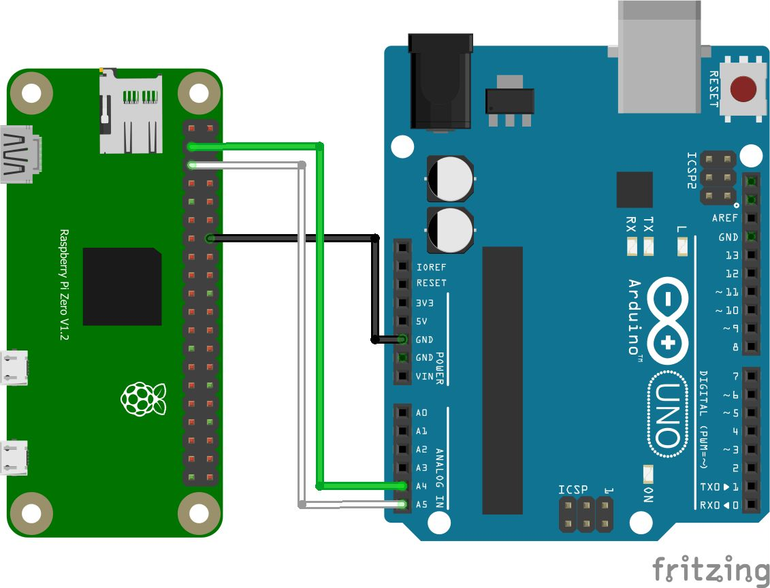
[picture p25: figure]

- Distributed Computing

## Why ROS?

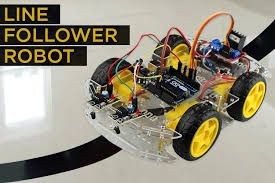
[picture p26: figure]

- Do not reinvent the wheel

## Why ROS?


- Rapid Testing

## Why ROS?


## Why ROS?

- Industry Ready

## Robotics Research


## Robotics Research


## Robotics Research


## Robotics Research


## ROS BASIC CONCEPTS


## ROS1 vs ROS2


- Windows Support in ROS2!
- No ROS Master
- Faster
- Architecture

## ROS2 Distributions


- We’ll use ROS2 Humble Hawksbill

## ROS Nodes & Topics

- Nodes can send / receive data
- Via Topics
- Send = Publish to Topic
- Receive = Subscribe to Topic


## ROS Nodes & Topics


- Flexible Structure!
- Robots typically have many Nodes & Topics

## ROS Nodes & Topics


- Nodes
  - talker
  - listener
- Topic
  - chatter

## ROS Nodes & Topics

- Nodes
  - teleop_turtle
  - turtle_sim
- Topics
  - turtle1/cmd_vel
  - …/feedback
  - …/status

## Setting Up ROS (Docker)


Prerequisites:
- Docker
Setup:
- Follow instructions here (https://hub.docker.com/r/codewithlennylen/rdj-2024)

## rdj-2024


## Resources

- What (https://medium.com/schmiedeone/what-is-ros-robot-operating-system-1aab3923dda5) (https://medium.com/schmiedeone/what-is-ros-robot-operating-system-1aab3923dda5)is (https://medium.com/schmiedeone/what-is-ros-robot-operating-system-1aab3923dda5) (https://medium.com/schmiedeone/what-is-ros-robot-operating-system-1aab3923dda5)ROS? (https://medium.com/schmiedeone/what-is-ros-robot-operating-system-1aab3923dda5)
- History (https://www.theconstruct.ai/history-ros/) (https://www.theconstruct.ai/history-ros/)of (https://www.theconstruct.ai/history-ros/) (https://www.theconstruct.ai/history-ros/)ROS (https://www.theconstruct.ai/history-ros/)
- Companies (https://github.com/vmayoral/ros-robotics-companies) (https://github.com/vmayoral/ros-robotics-companies)using (https://github.com/vmayoral/ros-robotics-companies) (https://github.com/vmayoral/ros-robotics-companies)ROS (https://github.com/vmayoral/ros-robotics-companies)
- ROS1 (https://www.model-prime.com/blog/ros-1-vs-ros-2-what-are-the-biggest-differences) (https://www.model-prime.com/blog/ros-1-vs-ros-2-what-are-the-biggest-differences)vs (https://www.model-prime.com/blog/ros-1-vs-ros-2-what-are-the-biggest-differences) (https://www.model-prime.com/blog/ros-1-vs-ros-2-what-are-the-biggest-differences)ROS2 (https://www.model-prime.com/blog/ros-1-vs-ros-2-what-are-the-biggest-differences)
- Changes (https://design.ros2.org/articles/changes.html) (https://design.ros2.org/articles/changes.html)between (https://design.ros2.org/articles/changes.html) (https://design.ros2.org/articles/changes.html)ROS1 (https://design.ros2.org/articles/changes.html) (https://design.ros2.org/articles/changes.html)and (https://design.ros2.org/articles/changes.html) (https://design.ros2.org/articles/changes.html)ROS2 (https://design.ros2.org/articles/changes.html)
- ROS2 (https://www.ros.org/reps/rep-2000.html) (https://www.ros.org/reps/rep-2000.html)Releases (https://www.ros.org/reps/rep-2000.html)
- How (https://roboticsbackend.com/how-to-learn-ros2/) (https://roboticsbackend.com/how-to-learn-ros2/)to (https://roboticsbackend.com/how-to-learn-ros2/) (https://roboticsbackend.com/how-to-learn-ros2/)Learn (https://roboticsbackend.com/how-to-learn-ros2/) (https://roboticsbackend.com/how-to-learn-ros2/)ROS2 (https://roboticsbackend.com/how-to-learn-ros2/)
- Getting (https://medium.com/schmiedeone/getting-started-with-ros2-part-1-d4c3b7335c71) (https://medium.com/schmiedeone/getting-started-with-ros2-part-1-d4c3b7335c71)Started (https://medium.com/schmiedeone/getting-started-with-ros2-part-1-d4c3b7335c71) (https://medium.com/schmiedeone/getting-started-with-ros2-part-1-d4c3b7335c71)with (https://medium.com/schmiedeone/getting-started-with-ros2-part-1-d4c3b7335c71) (https://medium.com/schmiedeone/getting-started-with-ros2-part-1-d4c3b7335c71)ROS2 (https://medium.com/schmiedeone/getting-started-with-ros2-part-1-d4c3b7335c71)
- ROS2 (https://docs.ros.org/en/humble/index.html) (https://docs.ros.org/en/humble/index.html)Humble (https://docs.ros.org/en/humble/index.html) Documentation (https://docs.ros.org/en/humble/index.html)


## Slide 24


- Thanks for your Attention

ROBOTICS DOJO 2024

- Lenny Ng’ang’a
- Robotics Researcher
- codewithlennylen254@gmail.com

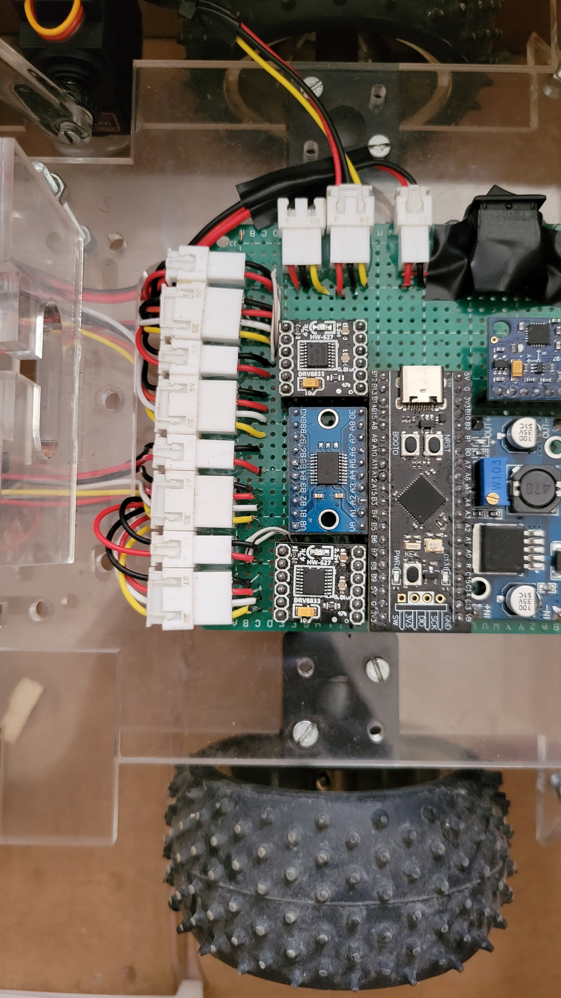
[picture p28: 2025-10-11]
circuit-loops-removed.jpg

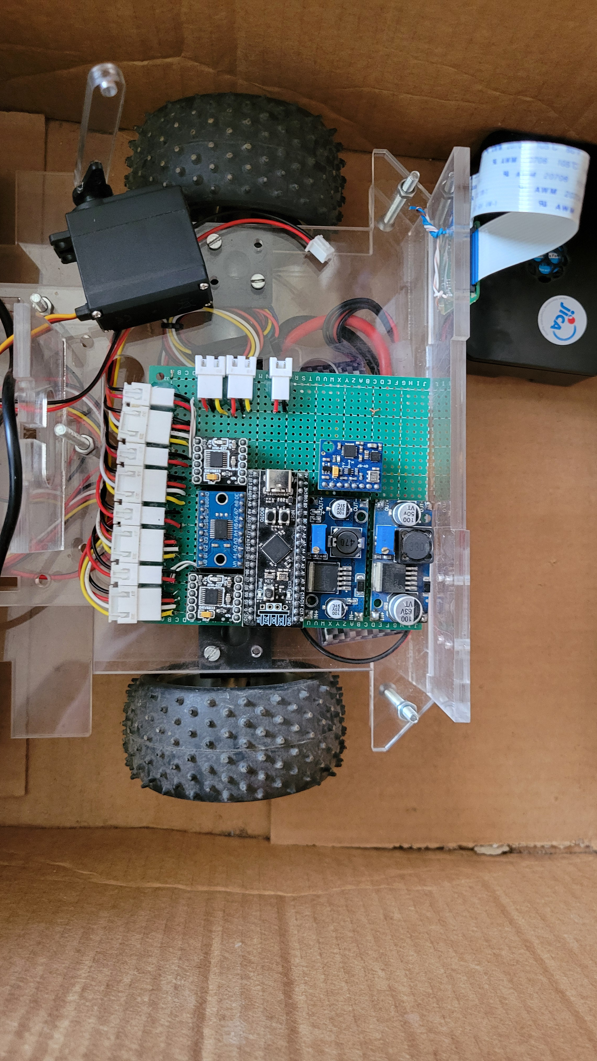
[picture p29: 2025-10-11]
circuit.jpg

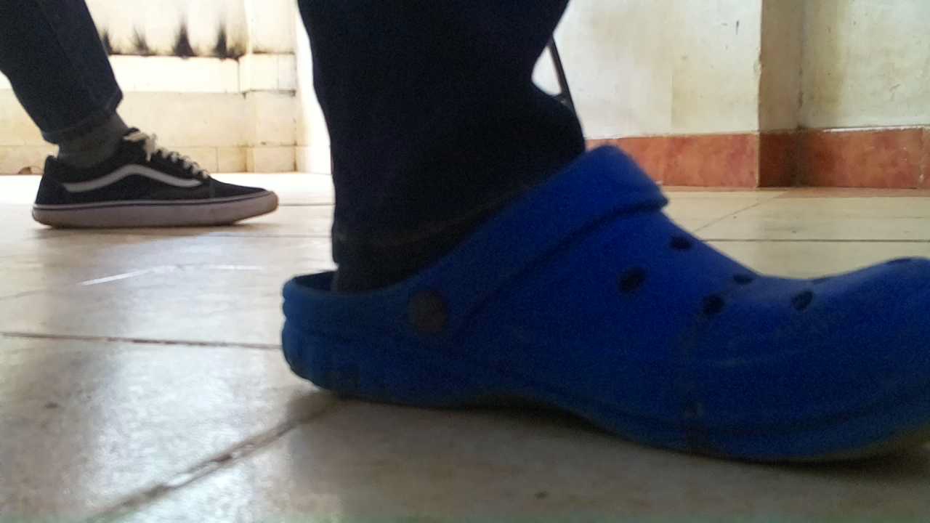
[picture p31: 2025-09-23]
pi-code/src/rdj2025_potato_disease_detection/rdj2025_potato_disease_detection/potato_leaf_20250923_121511.jpg

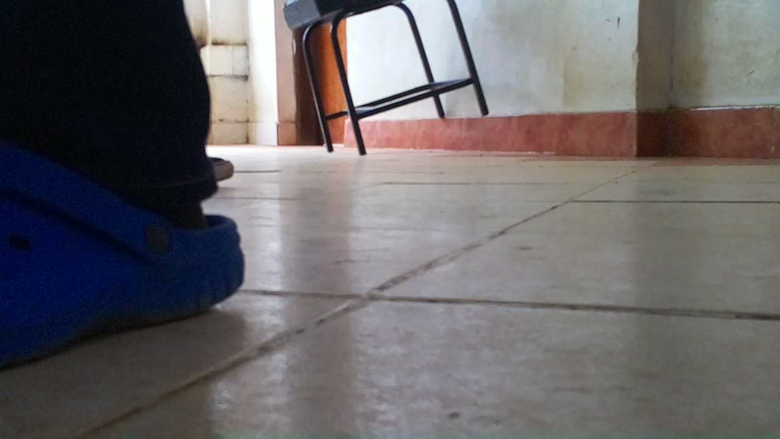
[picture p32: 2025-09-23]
pi-code/src/rdj2025_potato_disease_detection/rdj2025_potato_disease_detection/potato_leaf_20250923_121628.jpg

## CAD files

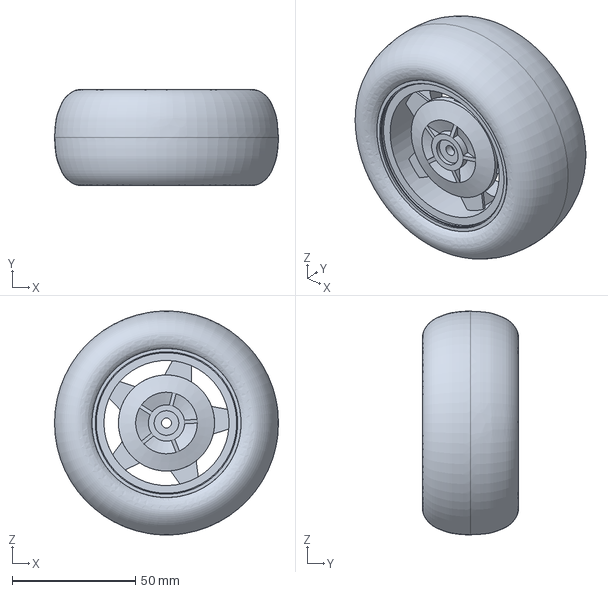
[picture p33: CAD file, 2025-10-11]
CAD/wheel/smooth-wheel-realistic.stp
90.9 x 38.9 x 90.8 mm

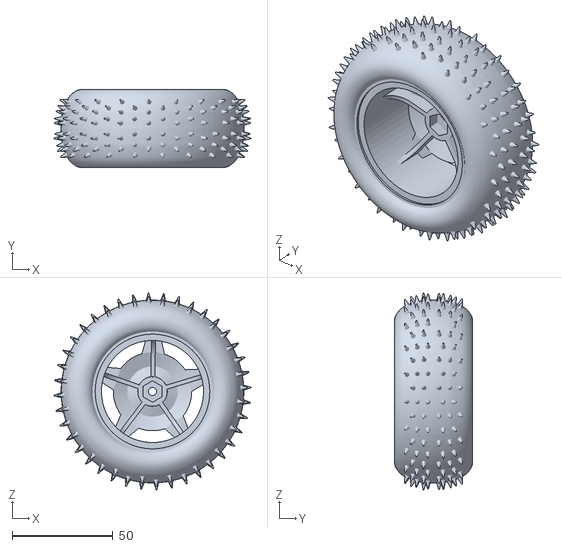
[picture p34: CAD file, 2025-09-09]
pi-code/src/jkl/description/meshes/front_left.stl
97.9 x 38.9 x 97.9

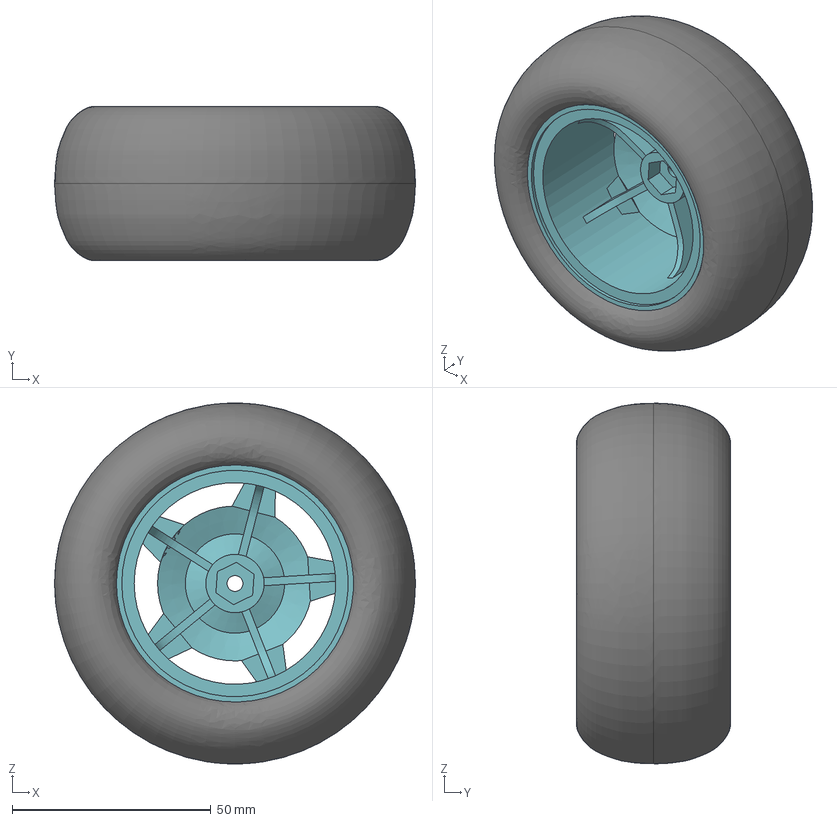
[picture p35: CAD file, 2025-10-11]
CAD/wheel/smooth-wheel-realistic-left.stp
90.9 x 38.9 x 90.8 mm

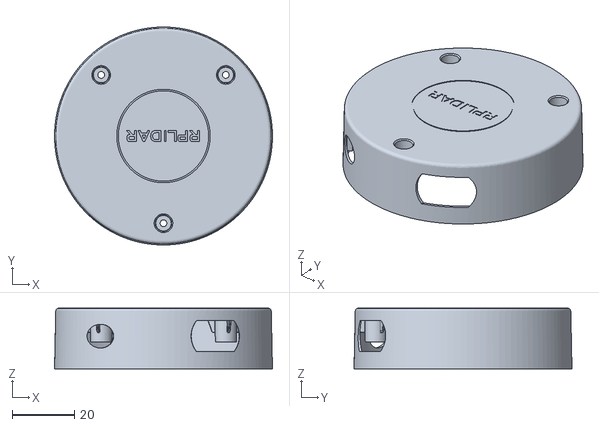
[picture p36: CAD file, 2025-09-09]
pi-code/src/jkl/description/meshes/lidar_link.stl
70.0 x 70.0 x 19.5

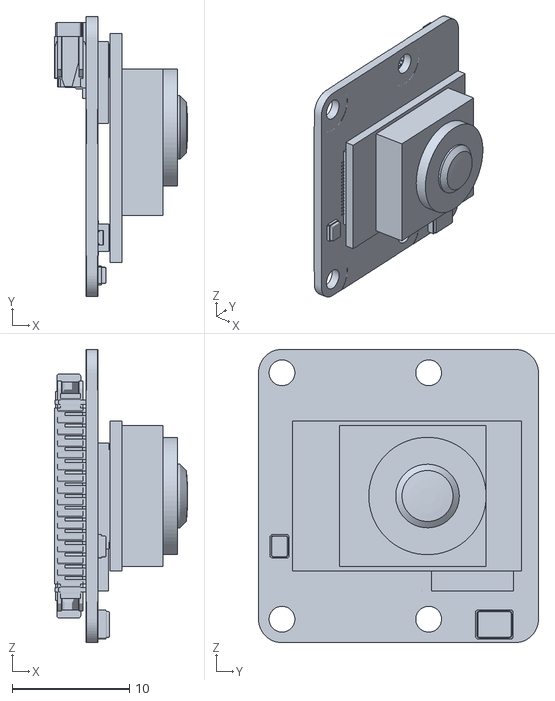
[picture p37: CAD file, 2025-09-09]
pi-code/src/jkl/description/meshes/camera_link.stl
11.3 x 23.9 x 25.0

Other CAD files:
pi-code/src/jkl/description/meshes/back_right.stl
pi-code/src/jkl/description/meshes/front_right.stl
pi-code/src/jkl/description/meshes/back_left.stl
CAD/Full-Assembly.iam
CAD/Full-Assembly.ipn
CAD/RP-lidar-A1/RP-lidar-A1.iam
CAD/RP-lidar-A1/Woodscrews_GB_TYPE136 M2X6-N.ipt
CAD/RP-lidar-A1/base.ipt
CAD/RP-lidar-A1/bottom-lid.ipt
CAD/RP-lidar-A1/connector-1_25-3pin.ipt
CAD/RP-lidar-A1/connector-1_25-4pin.ipt
CAD/RP-lidar-A1/connector-7pin-2_5.ipt
CAD/RP-lidar-A1/detector-mount.ipt
CAD/RP-lidar-A1/detector.ipt
CAD/RP-lidar-A1/devboard.ipt
CAD/RP-lidar-A1/head-base.ipt
CAD/RP-lidar-A1/head.ipt
CAD/RP-lidar-A1/laser-mount.ipt
CAD/RP-lidar-A1/laser.ipt
CAD/RP-lidar-A1/motherboard.ipt
CAD/RP-lidar-A1/motor-board.ipt
CAD/RP-lidar-A1/motor.ipt
CAD/RP-lidar-A1/rubber.ipt
CAD/RP-lidar-A1/stand-8x2.ipt
CAD/RP-lidar-A1/stand_15x2.ipt
CAD/RP-lidar-A1/wheel.ipt
CAD/bed-hinge.ipt
CAD/bed.ipt
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

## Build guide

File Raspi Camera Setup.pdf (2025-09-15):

# Raspberry Pi Camera Setup on Ubuntu 22.04 LTS (Pi 4)

This guide explains how to set up and use the Raspberry Pi Camera Module with Ubuntu 22.04 LTS on a Raspberry Pi 4 using rpicam-apps.

# Hardware Setup

Connect the Raspberry Pi Camera Module to the CSI port on the Raspberry Pi 4.

# System Preparation

### Update and upgrade the system:

sudo apt update
sudo apt upgrade -y

### Install general build tools:

sudo apt install -y git build-essential meson ninja-build pkg-config cmake

### Install libraries required for rpicam-apps:

sudo apt install -y libboost-dev libdrm-dev libexif-dev libjpeg-dev libpng-dev libtiff-dev
libudev-dev libyaml-dev python3-yaml python3-pip libgstreamer1.0-dev libgstreamer-plugins-base1.0-dev
libevent-dev libepoxy-dev libglib2.0-dev python3-ply

# Handling Missing Dependencies

### If you encounter missing dependencies, install them as follows:

1.

## Install Meson

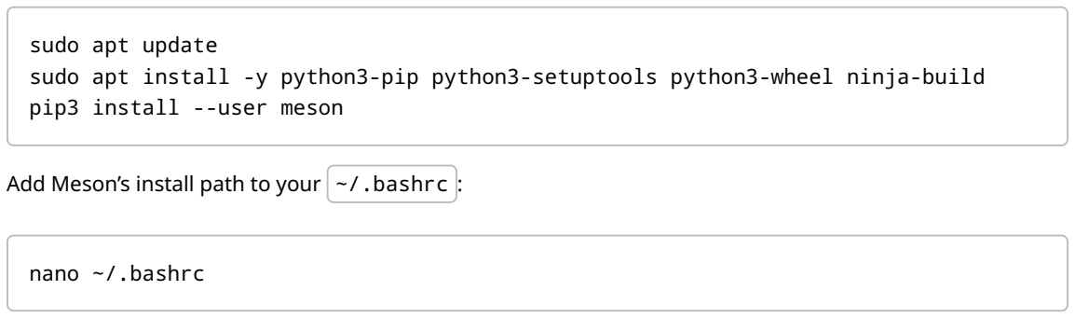
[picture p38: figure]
sudo apt update; pip3 install --user meson; nano ~/.bashrc

sudo apt install -y python3-pip python3-setuptools python3-wheel ninja-build

### Add Meson’s install path to your ~/.bashrc :

### Add this line at the end:

export PATH="$HOME/.local/bin:$PATH"

### Then reload:

source ~/.bashrc

## Fix ROS2 Keyring Issues

### If you see configuration issues with signed-by options:

sudo curl -sSL https://raw.githubusercontent.com/ros/rosdistro/master/ros.key -o /usr/share/keyrings/ros-archive-keyring.gpg
sudo chmod a+r /usr/share/keyrings/ros-archive-keyring.gpg

# Build and Install rpicam-apps

Clone and build rpicam-apps (which uses libcamera internally but provides Pi-specific utilities):

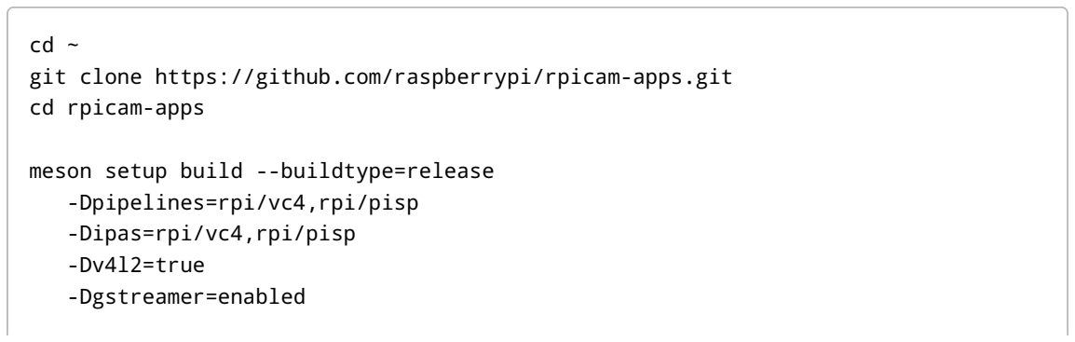
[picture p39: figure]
cd ~ git clone https://github.com/raspberrypi/rpicam-apps.git cd rpicam-apps; meson setup build --buildtype=release -Dpipelines=rpi/vc4,rpi/pisp -Dipas=rpi/vc4,rpi/pisp -Dv4l2=true -Dgstreamer=enabled
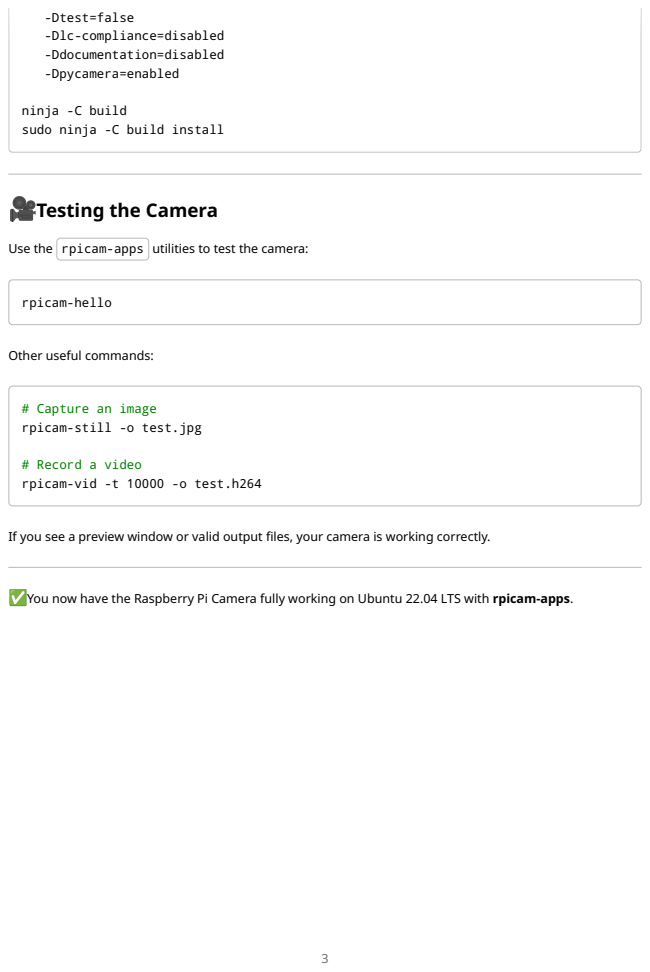
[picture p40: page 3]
rpicam-hello

-Dtest=false
-Dlc-compliance=disabled
-Ddocumentation=disabled
-Dpycamera=enabled

ninja -C build
sudo ninja -C build install

Testing the Camera

Use the rpicam-apps utilities to test the camera:

Other useful commands:

# Capture an image
rpicam-still -o test.jpg

# Record a video
rpicam-vid -t 10000 -o test.h264

If you see a preview window or valid output files, your camera is working correctly.

You now have the Raspberry Pi Camera fully working on Ubuntu 22.04 LTS with rpicam-apps.

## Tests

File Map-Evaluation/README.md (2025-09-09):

# Map Evaluator

## How to run

```
$ python map_evaluator.py <input_file>
```
Sample usage

```
$ ./map_evaluation.py maps/ipic_save.pgm
Similarity: 0.684662940491147
```

## Original README.md

Edit the map_evaluation.py at ```line 70``` and input the paths to the images. The first map is the generated map while the second path denotes the standard map

### TODO
- Make it so that the file names can be passed as arguments
- Improve the script to take better care of homography
- Improve the script for better accuracy

### Known issues
- The maps are rescaled to 120 x 60 which may result in accuracy loss

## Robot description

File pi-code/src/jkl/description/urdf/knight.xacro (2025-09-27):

<?xml version="1.0"?>
<robot name="knight" xmlns:xacro="http://www.ros.org/wiki/xacro">

<xacro:include filename="materials.xacro" />
<xacro:include filename="knight.trans" />
<xacro:include filename="knight.gazebo" />

<!-- BASE LINK -->

    <link name="base_link">
    </link>

    <!-- BASE_FOOTPRINT LINK -->

    <joint name="base_footprint_joint" type="fixed">
        <parent link="base_link" />
        <child link="base_footprint" />
        <origin xyz="0 0 0" rpy="0 0 0" />
    </joint>

    <link name="base_footprint">
    </link>

<link name="chassis">
  <inertial>
    <origin xyz="-0.019247214224469626 -0.009218676459717027 -0.0016402160280328" rpy="0 0 0"/>
    <mass value="1.8335875472772791"/>
    <inertia ixx="0.006149" iyy="0.014893" izz="0.017874" ixy="0.000425" iyz="6.7e-05" ixz="-0.000694"/>
  </inertial>
  <visual>
    <origin xyz="0 0 0" rpy="0 0 0"/>
    <geometry>
      <mesh filename="package://jkl/description/meshes/base_link.stl" scale="0.001 0.001 0.001"/>
    </geometry>
    <material name="silver"/>
  </visual>
  <collision>
    <origin xyz="0 0 0" rpy="0 0 0"/>
    <geometry>
      <mesh filename="package://jkl/description/meshes/base_link.stl" scale="0.001 0.001 0.001"/>
    </geometry>
  </collision>
</link>

<link name="camera_link">
  <inertial>
    <origin xyz="0.0022369050920157674 0.01190723740756753 -0.0106640979739921" rpy="0 0 0"/>
    <mass value="0.0018917728244253016"/>
    <inertia ixx="0.0" iyy="0.0" izz="0.0" ixy="0.0" iyz="0.0" ixz="-0.0"/>
  </inertial>
  <visual>
    <origin xyz="-0.110529 -0.039646 -0.024004" rpy="0 0 0"/>
    <geometry>
      <mesh filename="package://jkl/description/meshes/camera_link.stl" scale="0.001 0.001 0.001"/>
    </geometry>
    <material name="silver"/>
  </visual>
  <collision>
    <origin xyz="-0.110529 -0.039646 -0.024004" rpy="0 0 0"/>
    <geometry>
      <mesh filename="package://jkl/description/meshes/camera_link.stl" scale="0.001 0.001 0.001"/>
    </geometry>
  </collision>
</link>

<link name="laser_frame">
  <inertial>
    <origin xyz="-0.00013026516237509694 0.000607970103502142 0.014307371775280256" rpy="0 0 0"/>
    <mass value="0.007170751079753124"/>
    <inertia ixx="3e-06" iyy="3e-06" izz="6e-06" ixy="-0.0" iyz="0.0" ixz="-0.0"/>
  </inertial>
  <visual>
    <origin xyz="-0.044064 0.006954 -0.072354" rpy="0 0 0"/>
    <geometry>
      <mesh filename="package://jkl/description/meshes/lidar_link.stl" scale="0.001 0.001 0.001"/>
    </geometry>
    <material name="silver"/>
  </visual>
  <collision>
    <origin xyz="-0.044064 0.006954 -0.072354" rpy="0 0 0"/>
    <geometry>
      <mesh filename="package://jkl/description/meshes/lidar_link.stl" scale="0.001 0.001 0.001"/>
    </geometry>
  </collision>
</link>

<link name="front_right">
  <inertial>
    <origin xyz="-1.5497830999564033e-06 0.003510779818395135 1.9940828647688202e-06" rpy="0 0 0"/>
    <mass value="0.13957427599234848"/>
    <inertia ixx="0.000102" iyy="0.000178" izz="0.000102" ixy="-0.0" iyz="0.0" ixz="-0.0"/>
  </inertial>
  <visual>
    <origin xyz="-0.035729 0.118178 0.032546" rpy="0 0 0"/>
    <geometry>
      <mesh filename="package://jkl/description/meshes/front_right.stl" scale="0.001 0.001 0.001"/>
    </geometry>
    <material name="silver"/>
  </visual>
  <collision>
    <origin xyz="-0.035729 0.118178 0.032546" rpy="0 0 0"/>
    <geometry>
      <mesh filename="package://jkl/description/meshes/front_right.stl" scale="0.001 0.001 0.001"/>
    </geometry>
  </collision>
</link>

<link name="back_right">
  <inertial>
    <origin xyz="-1.5497830998106865e-06 0.0035107798183974387 1.994082864907598e-06" rpy="0 0 0"/>
    <mass value="0.13957427599234848"/>
    <inertia ixx="0.000102" iyy="0.000178" izz="0.000102" ixy="-0.0" iyz="0.0" ixz="-0.0"/>
  </inertial>
  <visual>
    <origin xyz="0.104271 0.118178 0.032546" rpy="0 0 0"/>
    <geometry>
      <mesh filename="package://jkl/description/meshes/back_right.stl" scale="0.001 0.001 0.001"/>
    </geometry>
    <material name="silver"/>
  </visual>
  <collision>
    <origin xyz="0.104271 0.118178 0.032546" rpy="0 0 0"/>
    <geometry>
      <mesh filename="package://jkl/description/meshes/back_right.stl" scale="0.001 0.001 0.001"/>
    </geometry>
  </collision>
</link>

<link name="front_left">
  <inertial>
    <origin xyz="-1.5493956658299557e-06 -0.00350998488597927 -1.4996934019281816e-06" rpy="0 0 0"/>
    <mass value="0.13957427599234848"/>
    <inertia ixx="0.000102" iyy="0.000178" izz="0.000102" ixy="0.0" iyz="0.0" ixz="0.0"/>
  </inertial>
  <visual>
    <origin xyz="-0.035329 -0.104198 0.032546" rpy="0 0 0"/>
    <geometry>
      <mesh filename="package://jkl/description/meshes/front_left.stl" scale="0.001 0.001 0.001"/>
    </geometry>
    <material name="silver"/>
  </visual>
  <collision>
    <origin xyz="-0.035329 -0.104198 0.032546" rpy="0 0 0"/>
    <geometry>
      <mesh filename="package://jkl/description/meshes/front_left.stl" scale="0.001 0.001 0.001"/> 
    </geometry>
  </collision>
</link>

<link name="back_left">
  <inertial>
    <origin xyz="-1.5493956658646502e-06 -0.003509984885977299 -1.4996934019281816e-06" rpy="0 0 0"/>
    <mass value="0.13957427599234848"/>
    <inertia ixx="0.000102" iyy="0.000178" izz="0.000102" ixy="0.0" iyz="0.0" ixz="0.0"/>
  </inertial>
  <visual>
    <origin xyz="0.104671 -0.104198 0.032546" rpy="0 0 0"/>
    <geometry>
      <mesh filename="package://jkl/description/meshes/back_left.stl" scale="0.001 0.001 0.001"/>
    </geometry>
    <material name="silver"/>
  </visual>
  <collision>
    <origin xyz="0.104671 -0.104198 0.032546" rpy="0 0 0"/>
    <geometry>
      <mesh filename="package://jkl/description/meshes/back_left.stl" scale="0.001 0.001 0.001"/>
    </geometry>
  </collision>
</link>

<!-- Joints -->
<joint name="camera_joint" type="fixed">
  <origin xyz="0.110529 0.039646 0.024004" rpy="0 0 0"/>
  <parent link="base_link"/>
  <child link="camera_link"/>
</joint>

<joint name="chassis_joint" type="fixed">
  <origin xyz="0.019247214224469626 0.009218676459717027 0.0016402160280328" rpy="0 0 0"/>
  <parent link="base_link"/>
  <child link="chassis"/>
</joint>

<joint name="lidar_joint" type="fixed">
  <origin xyz="0.044064 -0.006954 0.072354" rpy="0 0 0"/>
  <parent link="chassis"/>
  <child link="laser_frame"/>
</joint>

<joint name="front_right_joint" type="continuous">
  <origin xyz="0.035729 -0.118178 -0.032546" rpy="0 0 0"/>
  <parent link="base_link"/>
  <child link="front_right"/>
  <axis xyz="0.0 1.0 -0.0"/>
</joint>

<joint name="back_right_joint" type="continuous">
  <origin xyz="-0.104271 -0.118178 -0.032546" rpy="0 0 0"/>
  <parent link="base_link"/>
  <child link="back_right"/>
  <axis xyz="0.0 1.0 -0.0"/>
</joint>

<joint name="front_left_joint" type="continuous">
  <origin xyz="0.035329 0.104198 -0.032546" rpy="0 0 0"/>
  <parent link="base_link"/>
  <child link="front_left"/>
  <axis xyz="0.0 1.0 -0.0"/>
</joint>

<joint name="back_left_joint" type="continuous">
  <origin xyz="-0.104671 0.104198 -0.032546" rpy="0 0 0"/>
  <parent link="base_link"/>
  <child link="back_left"/>
  <axis xyz="0.0 1.0 -0.0"/>
</joint>

</robot>

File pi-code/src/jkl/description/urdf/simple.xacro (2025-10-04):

<?xml version="1.0"?>
<robot xmlns:xacro="http://www.ros.org/wiki/xacro">

    <xacro:include filename="inertial_macros.xacro" />


    <xacro:property name="chassis_length" value="0.290" />
    <xacro:property name="chassis_width" value="0.170" />
    <xacro:property name="chassis_height" value="0.036" />

    <xacro:property name="head_length" value="${chassis_length/2.5}" />
    <xacro:property name="head_width" value="${chassis_width*1.4}" />
    <xacro:property name="head_height" value="0.0448" />

    <xacro:property name="wheel_radius" value="0.0425" />
    <xacro:property name="wheel_thickness" value="0.038" />
    
    <xacro:property name="front_wheel_offset_x" value="${0.125 - wheel_radius}" />
    <xacro:property name="front_wheel_offset_y" value="${0.1024}" />
    <xacro:property name="front_wheel_offset_z" value="${wheel_radius}" />

    <xacro:property name="back_wheel_offset_x" value="${0.125 - wheel_radius}" />
    <xacro:property name="back_wheel_offset_y" value="${front_wheel_offset_y}" />
    <xacro:property name="back_wheel_offset_z" value="${front_wheel_offset_z}" />

    <xacro:property name="lidar_height" value="0.023" />
    <xacro:property name="lidar_offset_x" value="${front_wheel_offset_x + 0.02}" />
    <xacro:property name="lidar_offset_z" value="${chassis_height + head_height + front_wheel_offset_z}" />

    <xacro:property name="imu_length" value="0.030" />
    <xacro:property name="imu_width" value="0.015" />
    <xacro:property name="imu_offset_x" value="${front_wheel_offset_x + centre_of_rot_offset_x + imu_length/2 + 0.04}" />
    <xacro:property name="imu_offset_y" value="0.0" />
    <xacro:property name="imu_offset_z" value="${chassis_height + head_height + 0.02}" />

    <xacro:property name="chassis_mass" value="1.0" />
    <xacro:property name="lidar_mass" value="0.01" />
    <xacro:property name="head_mass" value="0.01" />
    <xacro:property name="imu_mass" value="0.001" />
    <xacro:property name="wheel_mass" value="0.05" />

    <xacro:property name="mu1" value="0.25" />
    <xacro:property name="mu2" value="0.25" />
    <xacro:property name="sl1" value="10.0" />
    <xacro:property name="sl2" value="10.0" />

    <xacro:property name="centre_of_rot_offset_x" value="${-0.02}" />

    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

    <link name="base_link">

    </link>

    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

    <joint name="base_footprint_joint" type="fixed">
        <parent link="base_link" />
        <child link="base_footprint" />
        <origin xyz="0 0 0" rpy="0 0 0" />
    </joint>

    <link name="base_footprint">
    </link>


    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

    <joint name="chassis_joint" type="fixed">
        <parent link="base_link" />
        <child link="chassis" />
        <origin xyz="${centre_of_rot_offset_x} 0 ${-front_wheel_offset_z}" />
    </joint>

    <link name="chassis">
        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
        <xacro:inertial_box mass="${chassis_mass}" x="${chassis_length}" y="${chassis_width}" z="${chassis_height}">
            <origin xyz="0 0 ${chassis_height/2 + front_wheel_offset_z}" rpy="0 0 0" />
        </xacro:inertial_box>
    </link>

    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


    <joint name="head_joint" type="fixed">
        <parent link="chassis" />
        <child link="head" />
        <origin xyz="${chassis_length/2 - head_length/2} 0 ${head_height/2 + front_wheel_offset_z}" />
    </joint>

    <link name="head">
        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
        <xacro:inertial_box mass="${head_mass}" x="${head_length}" y="${head_width}" z="${head_height}">
            <origin xyz="0 0 ${head_height}" rpy="0 0 0" />
        </xacro:inertial_box>
    </link>

    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


    <joint name="front_left_joint" type="continuous">
        <parent link="base_link" />
        <child link="front_left" />
        <origin xyz="${front_wheel_offset_x + centre_of_rot_offset_x} ${front_wheel_offset_y} 0" rpy="-${pi/2} 0 0" />
        <axis xyz="0 0 1" />
    </joint>

    <link name="front_left">
        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
        <xacro:inertial_cylinder mass="${wheel_mass}" length="${wheel_thickness}" radius="${wheel_radius}">
            <origin xyz="0 0 0" rpy="0 0 0" />
        </xacro:inertial_cylinder>
    </link>

    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


    <joint name="front_right_joint" type="continuous">
        <parent link="base_link" />
        <child link="front_right" />
        <origin xyz="${front_wheel_offset_x + centre_of_rot_offset_x} ${-front_wheel_offset_y} 0" rpy="${pi/2} 0 0" />
        <axis xyz="0 0 -1" />
    </joint>

    <link name="front_right">
        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
        <xacro:inertial_cylinder mass="${wheel_mass}" length="${wheel_thickness}" radius="${wheel_radius}">
            <origin xyz="0 0 0" rpy="0 0 0" />
        </xacro:inertial_cylinder>
    </link>

    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

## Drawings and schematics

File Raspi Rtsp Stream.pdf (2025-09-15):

# Raspberry Pi → Laptop RTSP Streaming (Ubuntu 22.04)

This guide describes a working, low‑lag RTSP streaming setup using a Raspberry Pi camera and MediaMTX as the RTSP server. It avoids the common failed to import fd DMA buffer errors and works well for real‑time applications like YOLO object detection.

## Requirements

Raspberry Pi running Ubuntu 22.04
Pi Camera Module (libcamera / rpicam‑apps installed) Laptop with ffplay (from ffmpeg ) or VLC installed Both devices connected to the same network

## Install and Start MediaMTX on the Pi

MediaMTX is a lightweight RTSP server.

sudo snap install mediamtx sudo snap start mediamtx

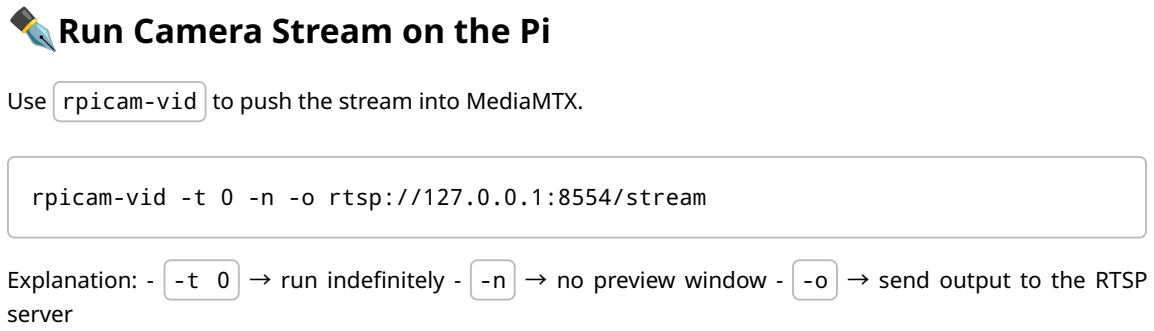
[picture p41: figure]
Run Camera Stream on the Pi; server

Use rpicam-vid to push the stream into MediaMTX.

rpicam-vid -t 0 -n -o rtsp://127.0.0.1:8554/stream

Explanation: - -t 0 → run indefinitely - -n → no preview window - -o → send output to the RTSP

## View Stream on Laptop

On the laptop, open the stream using ffplay or VLC. Replace <PI_IP> with the Raspberry Pi’s IP address.

•
•
•
•

1

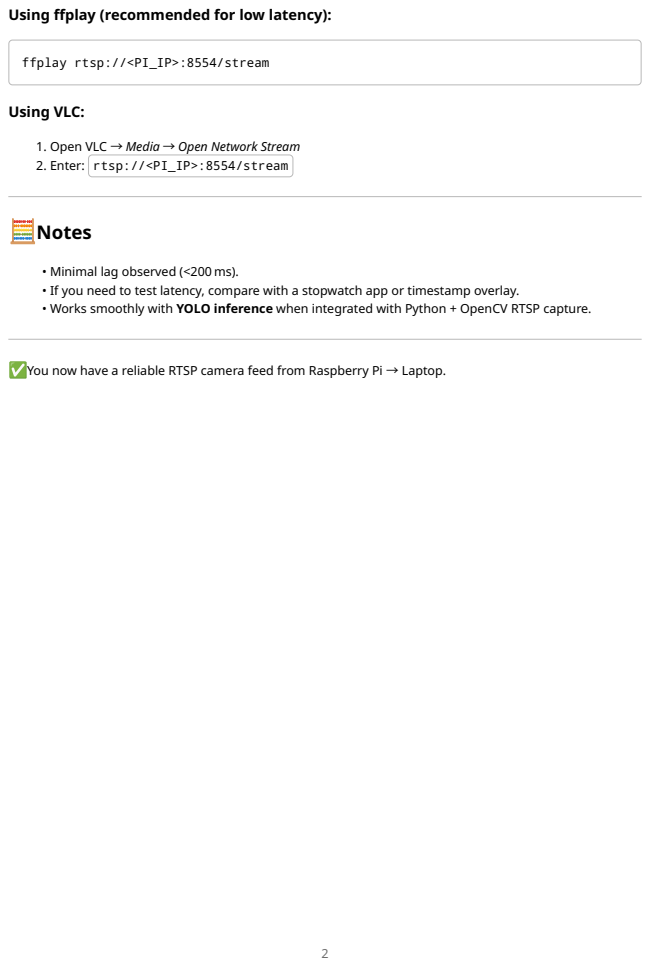
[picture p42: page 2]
Using VLC:; Notes

Using ffplay (recommended for low latency):

ffplay rtsp://<PI_IP>:8554/stream

Open VLC → Media → Open Network Stream
Enter: rtsp://<PI_IP>:8554/stream

Minimal lag observed (<200 ms).
If you need to test latency, compare with a stopwatch app or timestamp overlay.
Works smoothly with YOLO inference when integrated with Python + OpenCV RTSP capture.

You now have a reliable RTSP camera feed from Raspberry Pi → Laptop.

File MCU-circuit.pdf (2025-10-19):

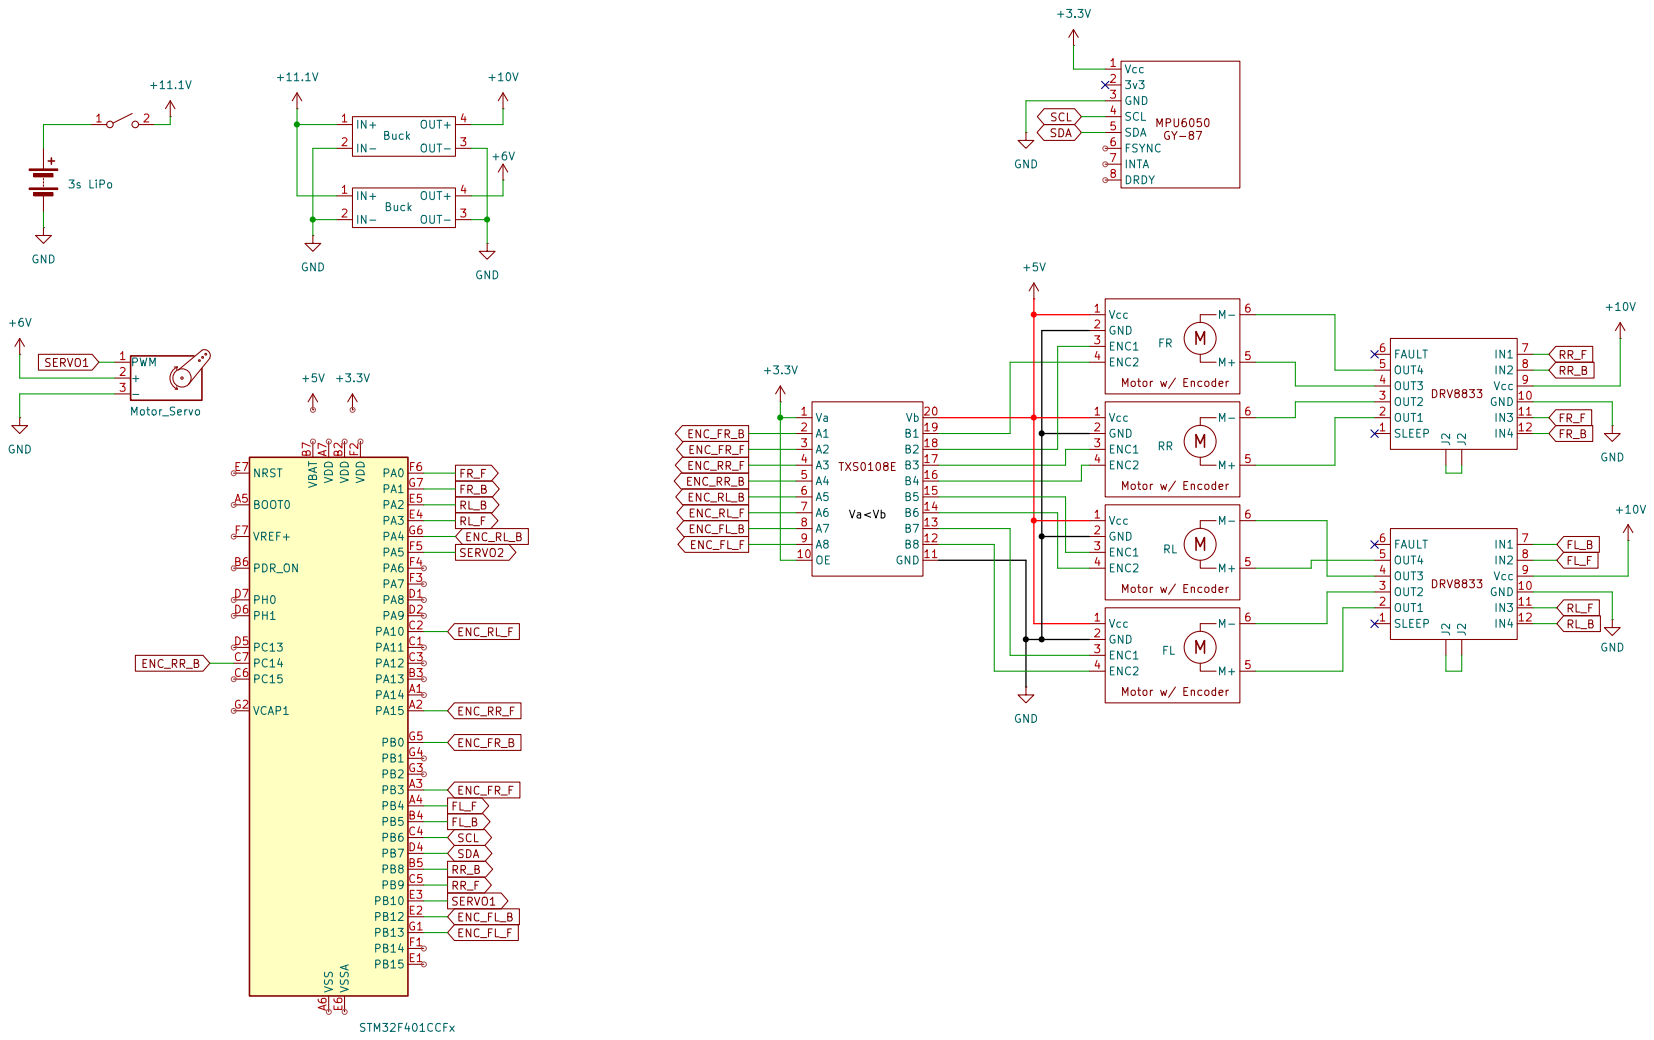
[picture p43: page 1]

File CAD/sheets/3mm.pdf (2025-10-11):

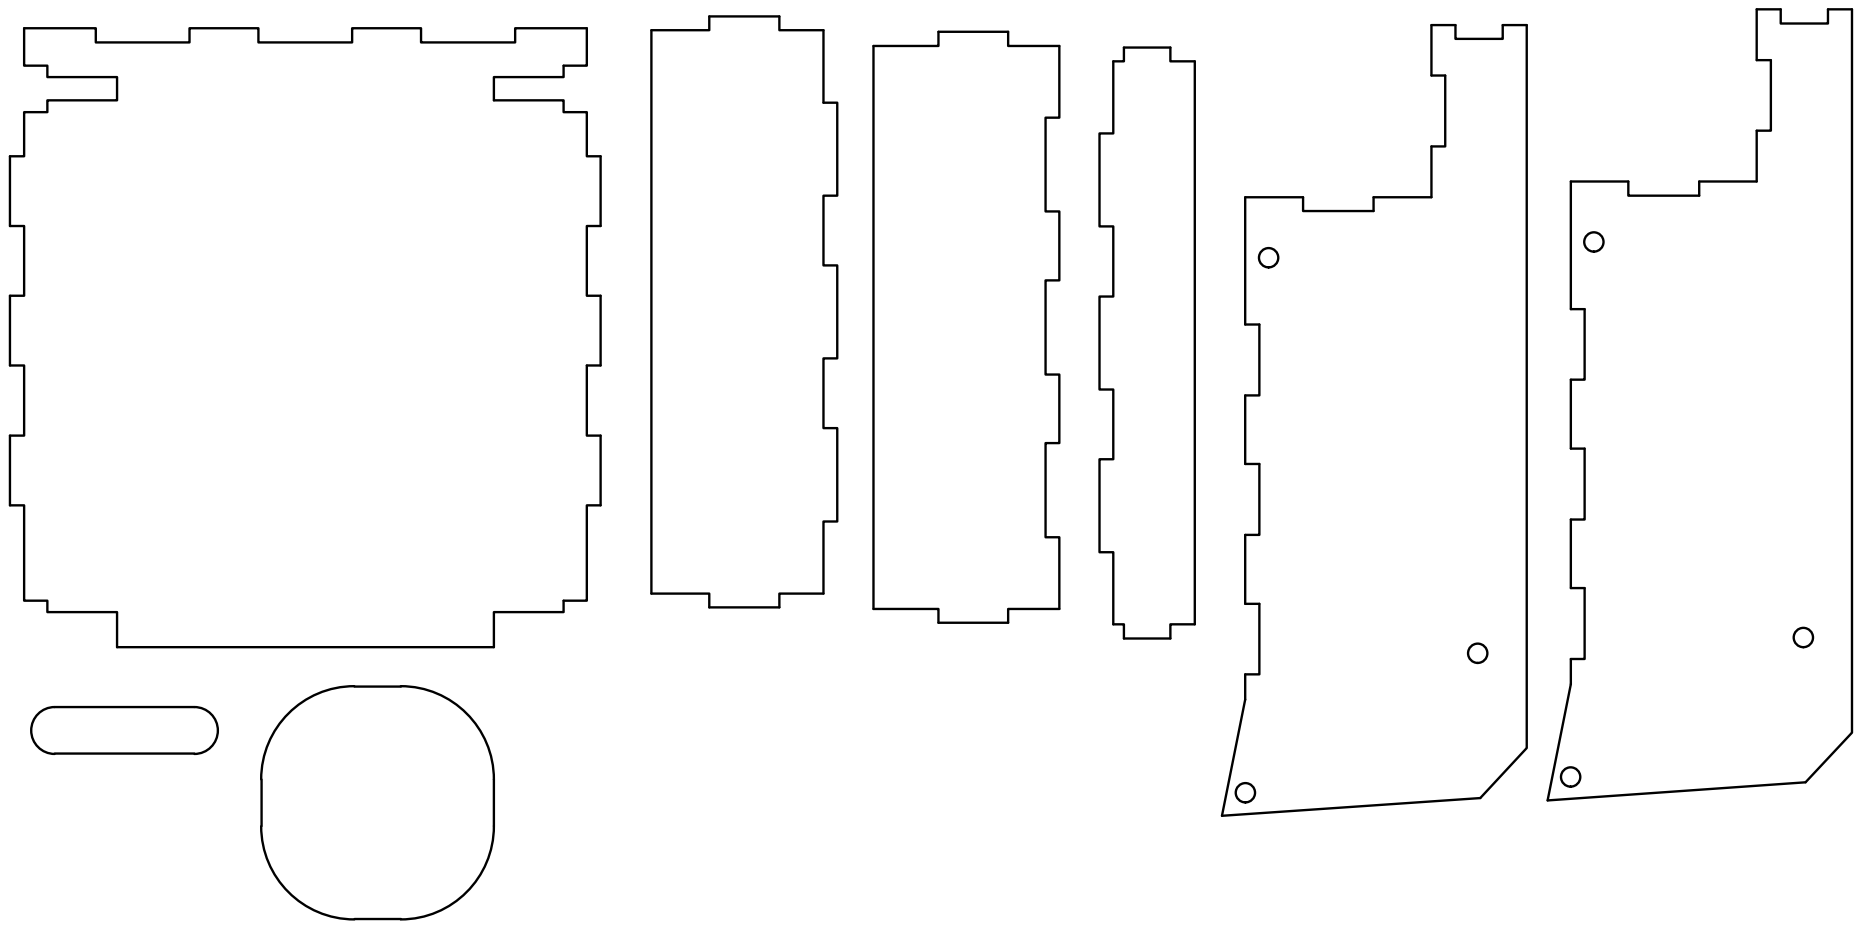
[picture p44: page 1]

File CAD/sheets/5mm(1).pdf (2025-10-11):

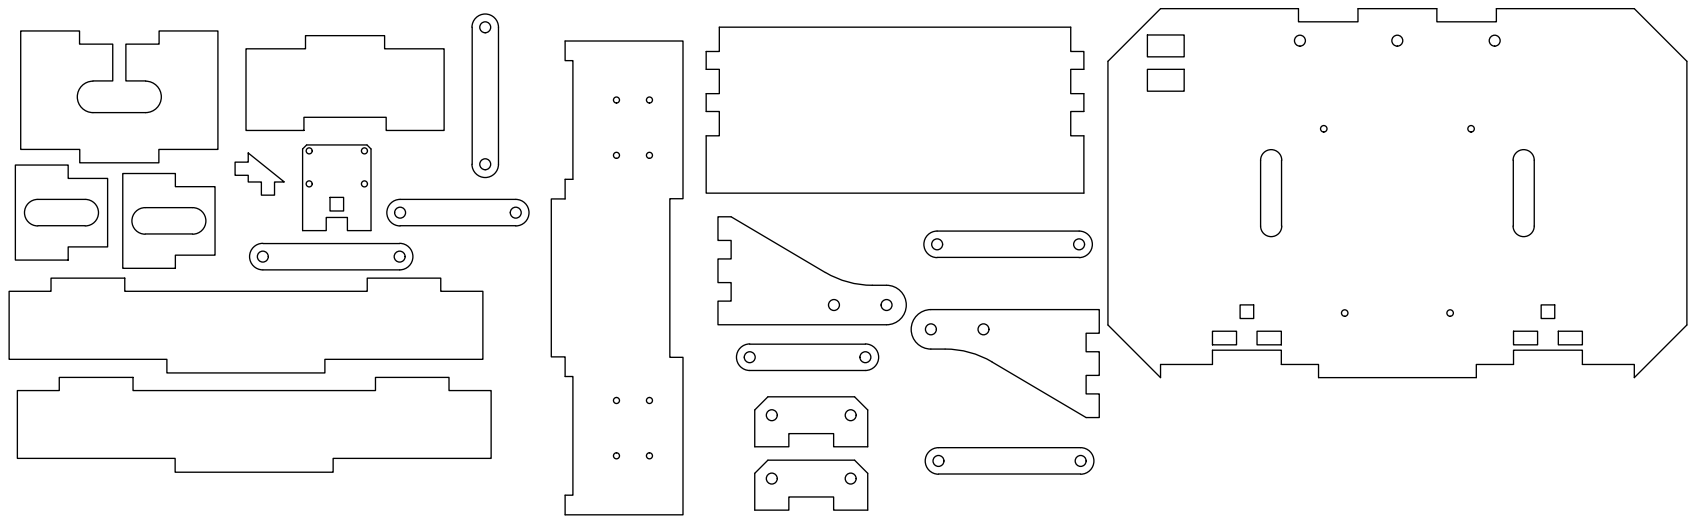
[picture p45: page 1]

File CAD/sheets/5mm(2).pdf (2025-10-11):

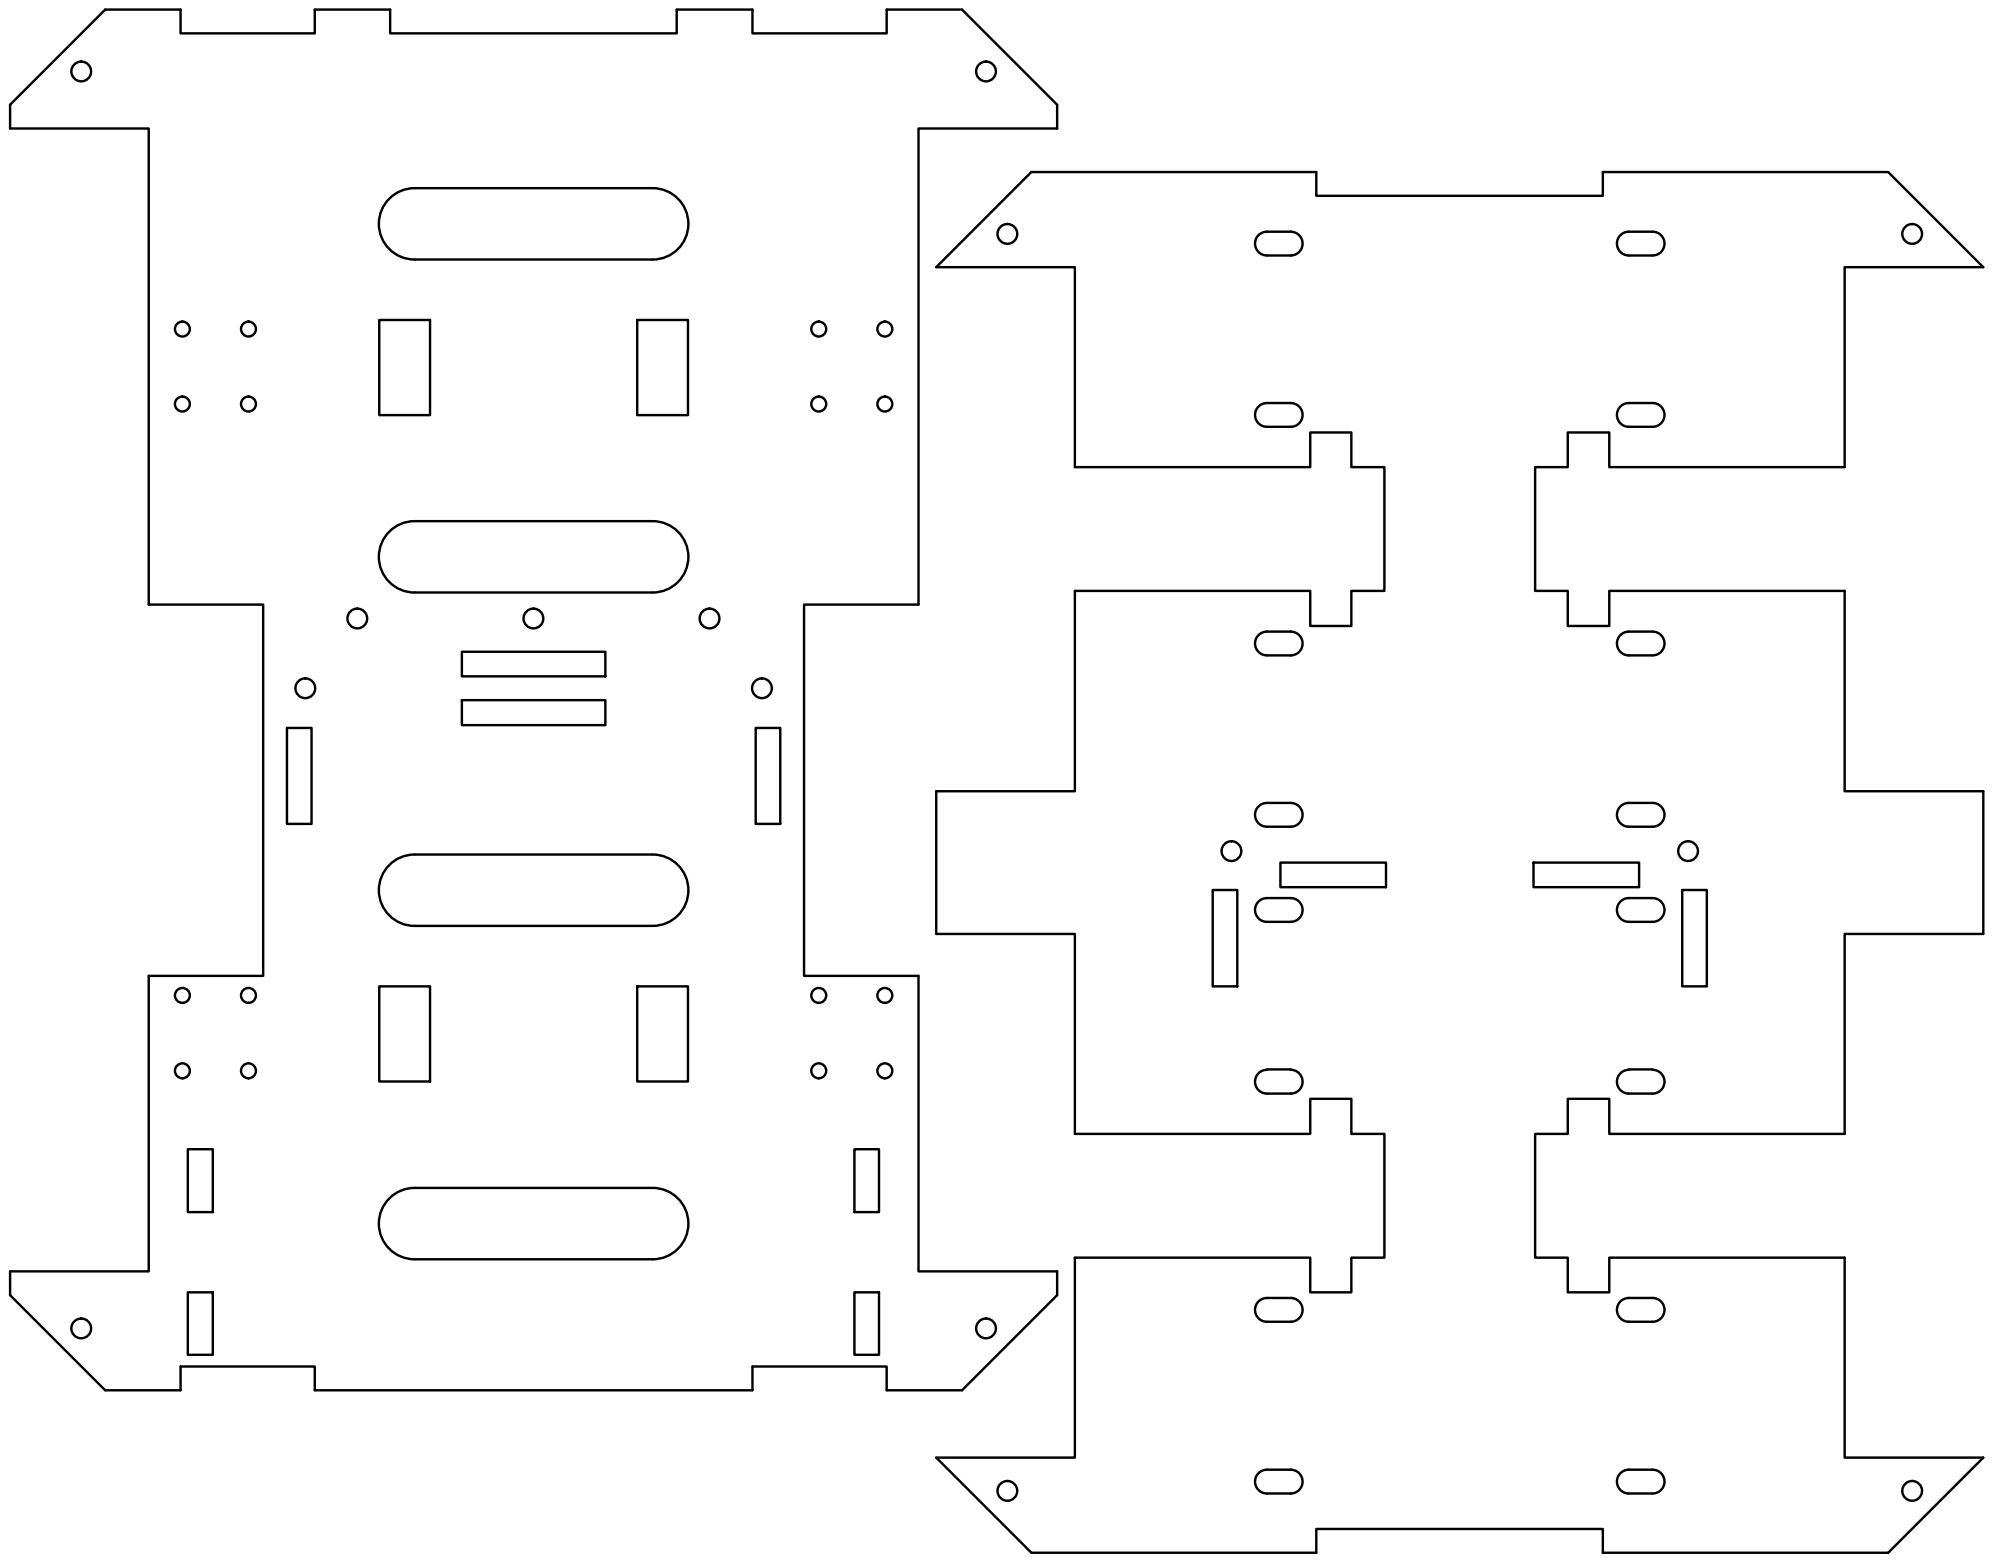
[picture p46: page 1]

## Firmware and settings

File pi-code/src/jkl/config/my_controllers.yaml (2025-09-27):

controller_manager:
  ros__parameters:
    update_rate: 30

    diff_cont:
      type: diff_drive_controller/DiffDriveController
    joint_broad:
      type: joint_state_broadcaster/JointStateBroadcaster
      joints: ['front_left_joint', 'front_right_joint', 'back_left_joint', 'back_right_joint']
    
    imu_broadcaster:
      type: imu_sensor_broadcaster/IMUSensorBroadcaster # https://control.ros.org/humble/doc/ros2_controllers/imu_sensor_broadcaster/doc/userdoc.html

    servo_controller:
      type: position_controllers/JointGroupPositionController # https://control.ros.org/humble/doc/ros2_controllers/position_controllers/doc/userdoc.html

imu_broadcaster:
  ros__parameters:
    sensor_name: imu_sensor # specified in HW interface
    frame_id: imu_link

    # static_covariance_linear_acceleration: [0.1, 0.0, 0.0,
    #                                         0.0, 0.1, 0.0,
    #                                         0.0, 0.0, 0.1]
    # static_covariance_angular_velocity: [0.1, 0.0, 0.0,
    #                                     0.0, 0.1, 0.0,
    #                                     0.0, 0.0, 0.1]
    # static_covariance_orientation: [-1.0, 0.0, 0.0,
    #                                 0.0, -1.0, 0.0,
    #                                 0.0, 0.0, -1.0]

servo_controller:
  ros__parameters:
    joints:
      - servo # specified in HW interface


diff_cont:
  ros__parameters:
    publish_rate: 50.0
    base_frame_id: base_link
    left_wheel_names: ['front_left_joint','back_left_joint']
    right_wheel_names: ['front_right_joint','back_right_joint']
    wheel_separation: 0.207
    wheel_radius: 0.0425
    wheels_per_side: 2

    use_stamped_vel: false

    odom_frame_id: odom
    enable_odom_tf: false


    # wheels_per_side: 2
    # wheel_separation_multiplier: 2
    # left_wheel_radius_multiplier: x
    # right_wheel_radius_multiplier: x

    # odom_frame_id: odom 
    # pose_covariance_diagonal: x
    # twist_covariance_diagonal: x
    # open_loop: x
    # enable_odom_tf: false 

    # cmd_vel_timeout: x
    # publish_limited_velocity: x
    # velocity_rolling_window_size: x
    

    # linear.x.has_velocity_limits: false
    # linear.x.has_acceleration_limits: false
    # linear.x.has_jerk_limits: false
    # linear.x.max_velocity: NAN
    # linear.x.min_velocity: NAN
    # linear.x.max_acceleration: NAN
    # linear.x.min_acceleration: NAN
    # linear.x.max_jerk: NAN
    # linear.x.min_jerk: NAN

    # angular.z.has_velocity_limits: false
    # angular.z.has_acceleration_limits: false
    # angular.z.has_jerk_limits: false
    # angular.z.max_velocity: NAN
    # angular.z.min_velocity: NAN
    # angular.z.max_acceleration: NAN
    # angular.z.min_acceleration: NAN
    # angular.z.max_jerk: NAN
    # angular.z.min_jerk: NAN




# joint_broad:
#   ros__parameters:

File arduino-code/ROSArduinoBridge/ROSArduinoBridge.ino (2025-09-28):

// 988 cpr

// python3 -m serial.tools.miniterm /dev/serial/by-id/usb-Arduino__www.arduino.cc__Arduino_Mega_2560_12148509806232150650-if00 57600 --echo
// python3 -m serial.tools.miniterm /dev/serial/by-id/usb-Silicon_Labs_CP2102_USB_to_UART_Bridge_Controller_0001-if00-port0 57600 --echo
// "/home/l/.arduino15/packages/arduino/tools/avrdude/6.3.0-arduino17/bin/avrdude" "-C/home/l/.arduino15/packages/arduino/tools/avrdude/6.3.0-arduino17/etc/avrdude.conf" -v -V -patmega2560 -cwiring "-P/dev/ttyACM0" -b115200 -D "-Uflash:w:/tmp/arduino/sketches/71D686EBAB249562A9FB6FE352DD37F9/ROSArduinoBridge.ino.hex:i"

/*
board - generic stm32f4 series
board part number - blackpill F401CC
Upload method - STM32Cube DFU
USB support generic CDC serial

Ensure no IO and no pin definitions on USB D+ and D- pins
*/

// issues
// occasional spikes on left wheel on new m value, seems when pid is not in use and motors were moved (perhaps by hand) the spikes occur, done?
// loading then releasing front left causes rear left to also spike, done?
// time delay before motors start moving for small values of m
// investigate the occasional spikes, done?
// investigate the occasional divergence on small values of m
// m 0 -50

// proposed changes
// add prevenc = enc in diff_controller when not moving
// add enc = readEnc in forFixingStartupSpikes in rosarduinobridge

#define USE_BASE  // Enable the base controller code
// #undef USE_BASE     // Disable the base controller code

#ifdef USE_BASE

#define OURENCODER

#define L298_MOTOR_DRIVER

// #define tuning_pid rearLeftPID  // comment this line to disable tuning mode

#endif

#define USE_SERVOS  // Enable use of PWM servos as defined in servos.h
// #undef USE_SERVOS  // Disable use of PWM servos

#define BAUDRATE 57600

// #define MAX_PWM 255
#define MAX_PWM 1023
// #define MAX_PWM 4095

#if defined(ARDUINO) && ARDUINO >= 100
#include "Arduino.h"
#else
#include "WProgram.h"
#endif

#include "commands.h"
#include "sensors.h"

#ifdef USE_SERVOS
#include "servos.h"
#endif

#ifdef USE_BASE

#include "motor_driver.h"
#include "encoder_driver.h"
#include "diff_controller.h"
#include "imu_driver.h"


#define PID_RATE 30  // Hz
// #define PID_RATE 50  // Hz
#define SENSOR_SAMPLERATE_DELAY_MS 30

/* Convert the rate into an interval */
const int PID_INTERVAL = 1000 / PID_RATE;

/* Track the next time we make a PID calculation */
unsigned long nextPID = PID_INTERVAL;

/* Stop the robot if it hasn't received a movement command
   in this number of milliseconds */
#define AUTO_STOP_INTERVAL 2000
long lastMotorCommand = AUTO_STOP_INTERVAL;
#endif

/* Variable initialization */

// A pair of varibles to help parse serial commands (thanks Fergs)
int arg = 0;
int inde_x = 0;

// Variable to hold an input character
char chr;

// Variable to hold the current single-character command
char cmd;

// Character arrays to hold the first and second arguments
char argv1[16];
char argv2[16];
char argv3[16];
char argv4[16];

// The arguments converted to integers
long arg1;
long arg2;
long arg3;
long arg4;


/* Clear the current command parameters */
void resetCommand() {
  cmd = '\0';
  memset(argv1, 0, sizeof(argv1));
  memset(argv2, 0, sizeof(argv2));
  memset(argv3, 0, sizeof(argv3));
  memset(argv4, 0, sizeof(argv4));
  arg1 = 0;
  arg2 = 0;
  arg3 = 0;
  arg4 = 0;

  arg = 0;
  inde_x = 0;
}

/* Run a command.  Commands are defined in commands.h */
void runCommand() {
  int i = 0;
  char *p = argv1;
  char *str;
  int pid_args[4];

  arg1 = atoi(argv1);
  arg2 = atoi(argv2);
  arg3 = atoi(argv3);
  arg4 = atoi(argv4);

  switch (cmd) {
    case GET_BAUDRATE:
      Serial.println(BAUDRATE);
      break;
    case ANALOG_READ:
      Serial.println(analogRead(arg1));
      break;
    case DIGITAL_READ:
      Serial.println(digitalRead(arg1));
      break;
    case ANALOG_WRITE:
      analogWrite(arg1, arg2);
      Serial.println("OK");
      break;
    case DIGITAL_WRITE:
      if (arg2 == 0)
        digitalWrite(arg1, LOW);
      else if (arg2 == 1)
        digitalWrite(arg1, HIGH);
      Serial.println("OK");
      break;
    case PIN_MODE:
      if (arg2 == 0)
        pinMode(arg1, INPUT);
      else if (arg2 == 1)
        pinMode(arg1, OUTPUT);
      Serial.println("OK");
      break;
    case PING:
      Serial.println(Ping(arg1));
      break;
#ifdef USE_SERVOS
    case SERVO_WRITE:
      servos[arg1].setTargetPosition(arg2);
      Serial.println("OK");
      break;
    case SERVO_READ:
      Serial.println(servos[arg1].getServo().read());
      break;
#endif

#ifdef USE_BASE
    case READ_ENCODERS:
      Serial.printf("%ld %ld %ld %ld\n", readEncoder(LEFT), readEncoder(RIGHT), readEncoder(REAR_LEFT), readEncoder(REAR_RIGHT));
      // Serial.printf("%ld %ld\n", readEncoder(LEFT), readEncoder(RIGHT));
      break;
    case RESET_ENCODERS:
      resetEncoders();
      resetPID();
      Serial.println("OK");
      break;
    case MOTOR_SPEEDS:
      /* Reset the auto stop timer */
      // Serial.printf("Setting motor speeds to %ld %ld %ld %ld\n", arg1, arg2, arg3, arg4);
      lastMotorCommand = millis();
      if (arg1 == 0 && arg2 == 0 && arg3 == 0 && arg4 == 0) {
        setMotorSpeeds(0, 0, 0, 0);
        resetPID();
        moving = 0;
      } else
        moving = 1;

      forFixingStartupKick();

      leftPID.TargetTicksPerFrame = arg1;
      rightPID.TargetTicksPerFrame = arg2;
      rearLeftPID.TargetTicksPerFrame = arg3;
      rearRightPID.TargetTicksPerFrame = arg4;

      Serial.println("OK");
      break;

    case MOTOR_RAW_PWM:
      // Serial.printf("Setting motor speeds to %ld %ld %ld %ld\n", arg1, arg2, arg3, arg4);
      /* Reset the auto stop timer */
      lastMotorCommand = millis();
      resetPID();
      moving = 0;  // Sneaky way to temporarily disable the PID
      setMotorSpeeds(arg1, arg2, arg3, arg4);
      Serial.println("OK");
      break;

    case UPDATE_PID:
      while ((str = strtok_r(p, ":", &p)) != nullptr) {
        pid_args[i] = atoi(str);
        i++;
      }

      Kp = pid_args[0];
      Kd = pid_args[1];
      Ki = pid_args[2];
      Ko = pid_args[3];
      Serial.println("OK");
      break;

    case GET_CURRENT_PID:
      Serial.printf("%d %d %d %d\n", Kp, Kd, Ki, Ko);
      break;

    case GO_FORWARD:
      lastMotorCommand = millis();
      setMotorSpeedsFeedback(60, 60, 60, 60);
      Serial.println("OK");
      break;

    case GO_BACKWARD:
      lastMotorCommand = millis();
      setMotorSpeedsFeedback(-60, -60, -60, -60);
      Serial.println("OK");
      break;

    case TURN_LEFT:
      lastMotorCommand = millis();
      setMotorSpeedsFeedback(-30, 30, -30, 30);
      Serial.println("OK");
      break;

    case TURN_RIGHT:
      lastMotorCommand = millis();
      setMotorSpeedsFeedback(30, -30, 30, -30);
      Serial.println("OK");
      break;

#endif
    case READ_IMU:
      // ax ay az gx gy gz
      Serial.print(mpuData.Ax);
      Serial.print(" ");
      Serial.print(mpuData.Ay);
      Serial.print(" ");
      Serial.print(mpuData.Az);
      Serial.print(" ");
      Serial.print(mpuData.Gx);
      Serial.print(" ");
      Serial.print(mpuData.Gy);
      Serial.print(" ");
      Serial.print(mpuData.Gz);
      Serial.print(" ");
      Serial.print(mpuData.Qw);
      Serial.print(" ");
      Serial.print(mpuData.Qx);
      Serial.print(" ");
      Serial.print(mpuData.Qy);
      Serial.print(" ");
      Serial.print(mpuData.Qz);
      Serial.println();
      break;
    default:
      Serial.println("Invalid Command Serial");
      break;
  }
}


/* Setup function--runs once at startup. */
void setup() {
  Serial.begin(BAUDRATE);

  // for detecting dfu mode
  pinMode(PC13, OUTPUT);
  digitalWrite(PC13, LOW);

// Initialize the motor controller if used */
#ifdef USE_BASE

#ifdef OURENCODER

  pinMode(FRONT_LEFT_ENC_PIN_A, INPUT);
  pinMode(FRONT_LEFT_ENC_PIN_B, INPUT);
  pinMode(FRONT_RIGHT_ENC_PIN_A, INPUT);
  pinMode(FRONT_RIGHT_ENC_PIN_B, INPUT);
  pinMode(REAR_LEFT_ENC_PIN_A, INPUT);
  pinMode(REAR_LEFT_ENC_PIN_B, INPUT);
  pinMode(REAR_RIGHT_ENC_PIN_A, INPUT);
  pinMode(REAR_RIGHT_ENC_PIN_B, INPUT);

  attachInterrupt(FRONT_LEFT_ENC_PIN_A, countFrontLShort, CHANGE);
  attachInterrupt(FRONT_RIGHT_ENC_PIN_A, countFrontRShort, CHANGE);
  attachInterrupt(REAR_LEFT_ENC_PIN_A, countRearLShort, CHANGE);
  attachInterrupt(REAR_RIGHT_ENC_PIN_A, countRearRShort, CHANGE);

#endif
  initMotorController();
  resetPID();
#endif

  /* Attach servos if used */
#ifdef USE_SERVOS
  int i;
  for (i = 0; i < N_SERVOS; i++) {
    servos[i].initServo(
      servoPins[i],
      stepDelay[i],
      servoInitPosition[i]);
  }
#endif

  initMPU6050();
}

/* Enter the main loop.  Read and parse input from the serial port
   and run any valid commands. Run a PID calculation at the target
   interval and check for auto-stop conditions.
*/
void loop() {

  while (Serial.available() > 0) {

    // Read the next character
    chr = Serial.read();

    // if (chr==10 || chr == 13) {  // terminate with \n or \r
    if (chr == 13) {  // terminate with \r
      if (arg == 1)
        argv1[inde_x] = '\0';
      else if (arg == 2)
        argv2[inde_x] = '\0';
      else if (arg == 3)
        argv3[inde_x] = '\0';
      else if (arg == 4)
        argv4[inde_x] = '\0';

      runCommand();
      resetCommand();

      while (Serial.available()) {  // to clear Serial buffer
        Serial.read();
      }
    }
    // Use spaces to delimit parts of the command
    else if (chr == ' ') {
      // Step through the arguments
      if (arg == 0)
        arg = 1;
      else if (arg == 1) {
        argv1[inde_x] = '\0';
        arg = 2;
        inde_x = 0;
      } else if (arg == 2) {
        argv2[inde_x] = '\0';
        arg = 3;
        inde_x = 0;
      } else if (arg == 3) {
        argv3[inde_x] = '\0';
        arg = 4;
        inde_x = 0;
      }
      continue;
    } else {

      if (arg == 0) {
        // The first arg is the single-letter command
        cmd = chr;
      } else if (arg == 1) {
        // Subsequent arguments can be more than one character
        argv1[inde_x] = chr;
        inde_x++;
      } else if (arg == 2) {
        argv2[inde_x] = chr;
        inde_x++;
      } else if (arg == 3) {
        argv3[inde_x] = chr;
        inde_x++;
      } else if (arg == 4) {
        argv4[inde_x] = chr;
        inde_x++;
      }
    }
  }

// If we are using base control, run a PID calculation at the appropriate intervals
#ifdef USE_BASE
  if (millis() > nextPID) {
    updatePID();
    nextPID += PID_INTERVAL;
  }

#ifndef tuning_pid
  // Check to see if we have exceeded the auto-stop interval
  if ((millis() - lastMotorCommand) > AUTO_STOP_INTERVAL) {
    setMotorSpeeds(0, 0, 0, 0);
    moving = 0;
  }
#endif

#endif

  static unsigned long mpuPub = 0;
  if (millis() - mpuPub > SENSOR_SAMPLERATE_DELAY_MS) {
    mpuPub = millis();
    updateMpu6050();
  }

// Sweep servos
#ifdef USE_SERVOS
  int i;
  for (i = 0; i < N_SERVOS; i++) {
    servos[i].doSweep();
  }
#endif

#ifdef tuning_pid
  forTuningPID();
  if (tuning_pid.TargetTicksPerFrame != 0)
    Serial.printf("%ld\n", tuning_pid.Encoder);
    // Serial.printf("%ld %d %d 0 80 \n", output, input, (int)tuning_pid.TargetTicksPerFrame);
    // Serial.printf("%ld %ld I %ld %ld %d %ld\n", Kp * Perror, Kd * (input - tuning_pid.PrevInput), tuning_pid.ITerm, output, (int)tuning_pid.TargetTicksPerFrame, input);
    // Pterm Dterm Iterm PWMval Target Actual
#endif

  // static unsigned long lastPrinted = 0;
  // if (millis() - lastPrinted > 20) {
  //   lastPrinted = millis();
  //   Serial.printf("%ld %ld %ld %ld\n", readEncoder(LEFT), readEncoder(RIGHT), readEncoder(REAR_LEFT), readEncoder(REAR_RIGHT));
  // }
}

// eliminates kick due to wheel movement since last PID loop.
// The kick comes because the encoder value is at the point
// when motor PWM becomes 0, not when the motors actually stop
void forFixingStartupKick() {
  // leftPID.Encoder = readEncoder(LEFT); // do not uncomment, it has an acceleration bug when driving
  // rightPID.Encoder = readEncoder(RIGHT); // do not uncomment, it has an acceleration bug when driving
  // rearLeftPID.Encoder = readEncoder(REAR_LEFT); // do not uncomment, it has an acceleration bug when driving
  // rearRightPID.Encoder = readEncoder(REAR_RIGHT); // do not uncomment, it has an acceleration bug when driving

  leftPID.PrevEnc = leftPID.Encoder;
  rightPID.PrevEnc = rightPID.Encoder;
  rearLeftPID.PrevEnc = rearLeftPID.Encoder;
  rearRightPID.PrevEnc = rearRightPID.Encoder;
}

#ifdef tuning_pid
// first send an m value then this function will do the rest
void forTuningPID() {

  // u 70:150:0:50 // tuned on 07/09/2925
  // u 320:10:0:60
  // u 100:70:0:20
  // u 100:75:1:20
  // u 105:75:1:22
  // u 105:80:1:18
  // u 105:80:1:20
  // u 110:85:1:10

  // u 500:260:0:50 // tuned on 08/09/2025
  // u 200:120:0:50
  // u 200:120:1:50

  // u 65:75:15:5 // for small signals
  // u 95:85:15:5
  // u 60:50:5:5
  // u 45:300:36:30 // diverges on small values

  // m 20 u 105:75:0:22 causes madness reducing Ko to 18 fixed it

  static unsigned long lastPID = 0;
  lastMotorCommand = millis();
  if (millis() - lastPID >= 2000) {
    lastPID = millis();
    moving = 1;

    leftPID.Encoder = readEncoder(LEFT);
    rightPID.Encoder = readEncoder(RIGHT);
    rearLeftPID.Encoder = readEncoder(REAR_LEFT);
    rearRightPID.Encoder = readEncoder(REAR_RIGHT);

    leftPID.PrevEnc = leftPID.Encoder;
    rightPID.PrevEnc = rightPID.Encoder;
    rearLeftPID.PrevEnc = rearLeftPID.Encoder;
    rearRightPID.PrevEnc = rearRightPID.Encoder;

    leftPID.TargetTicksPerFrame = 0;
    rightPID.TargetTicksPerFrame = 0;
    rearLeftPID.TargetTicksPerFrame = 0;
    rearRightPID.TargetTicksPerFrame = 0;

    tuning_pid.TargetTicksPerFrame = -tuning_pid.TargetTicksPerFrame;
  }
}

#endif

/*
// not related to project but might be useful in future
void runEvery(int interval, unsigned long* lastRunTime, void (*callback)()) {
  if (millis() < *lastRunTime + interval) {
    return;
  }
  *lastRunTime = millis();
  callback();
}
*/

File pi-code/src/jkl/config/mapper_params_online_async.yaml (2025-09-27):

slam_toolbox:
  ros__parameters:

    # Plugin params
    solver_plugin: solver_plugins::CeresSolver
    ceres_linear_solver: SPARSE_NORMAL_CHOLESKY
    ceres_preconditioner: SCHUR_JACOBI
    ceres_trust_strategy: LEVENBERG_MARQUARDT
    ceres_dogleg_type: TRADITIONAL_DOGLEG
    ceres_loss_function: None

    # ROS Parameters
    odom_frame: odom
    map_frame: map
    base_frame: base_footprint
    scan_topic: /scan
    use_map_saver: true
    mode: mapping
    # mode: localization

    # if you'd like to immediately start continuing a map at a given pose
    # or at the dock, but they are mutually exclusive, if pose is given
    # will use pose
    # map_file_name: f1
    # map_start_pose: [0.0, -0.1, 0.0]
    map_start_at_dock: true

    debug_logging: false
    throttle_scans: 1
    transform_publish_period: 0.05 #if 0 never publishes odometry
    map_update_interval: 0.4
    resolution: 0.05
    min_laser_range: 0.4 #  for rastering images
    max_laser_range: 12.0 #  for rastering images
    minimum_time_interval: 0.5
    transform_timeout: 0.2
    tf_buffer_duration: 30.
    stack_size_to_use: 40000000 # // program needs a larger stack size to serialize large maps
    enable_interactive_mode: true

    # General Parameters
    use_scan_matching: true
    use_scan_barycenter: true
    minimum_travel_distance: 0.5
    minimum_travel_heading: 0.5
    scan_buffer_size: 30
    scan_buffer_maximum_scan_distance: 15.0 # Maximum distance of a scan from the pose before removing the scan from the buffer
    link_match_minimum_response_fine: 0.1  
    link_scan_maximum_distance: 0.5 # **
    loop_search_maximum_distance: 6.0 # Maximum threshold of distance for scans to be considered for loop closure
    do_loop_closing: true 
    loop_match_minimum_chain_size: 10           
    loop_match_maximum_variance_coarse: 3.0  
    loop_match_minimum_response_coarse: 0.35    
    loop_match_minimum_response_fine: 0.45

    # Correlation Parameters - Correlation Parameters
    correlation_search_space_dimension: 0.5
    correlation_search_space_resolution: 0.01
    correlation_search_space_smear_deviation: 0.1 

    # Correlation Parameters - Loop Closure Parameters
    loop_search_space_dimension: 8.0
    loop_search_space_resolution: 0.05
    loop_search_space_smear_deviation: 0.03

    # Scan Matcher Parameters
    distance_variance_penalty: 0.5      
    angle_variance_penalty: 1.0    

    fine_search_angle_offset: 0.00349     
    coarse_search_angle_offset: 0.349   
    coarse_angle_resolution: 0.0349        
    minimum_angle_penalty: 0.9
    minimum_distance_penalty: 0.5
    use_response_expansion: true
    min_pass_through: 2
    occupancy_threshold: 0.1

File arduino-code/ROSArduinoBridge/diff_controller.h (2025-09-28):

#include "HardwareSerial.h"
/* Functions and type-defs for PID control.

   Taken mostly from Mike Ferguson's ArbotiX code which lives at:

   http://vanadium-ros-pkg.googlecode.com/svn/trunk/arbotix/
*/

/* PID setpoint info For a Motor */
typedef struct
{
  double TargetTicksPerFrame;  // target speed in ticks per frame
  long Encoder;                // encoder count
  long PrevEnc;                // last encoder count

  /*
   * Using previous input (PrevInput) instead of PrevError to avoid derivative kick,
   * see http://brettbeauregard.com/blog/2011/04/improving-the-beginner%E2%80%99s-pid-derivative-kick/
   */
  int PrevInput;  // last input
  // int PrevErr;    // last error

  /*
   * Using integrated term (ITerm) instead of integrated error (Ierror),
   * to allow tuning changes,
   * see http://brettbeauregard.com/blog/2011/04/improving-the-beginner%E2%80%99s-pid-tuning-changes/
   */
  // int Ierror;
  int ITerm;  // integrated term

  long output;  // last motor setting
} SetPointInfo;

SetPointInfo leftPID, rightPID, rearLeftPID, rearRightPID;

/* PID Parameters */
// default
// int Kp = 20;
// int Kd = 12;
// int Ki = 0;
// int Ko = 50;

// ours, MAX_PWM = 255
// int Kp = 70;
// int Kd = 150;
// int Ki = 0;
// int Ko = 50;

// ours, MAX_PWM = 1023
int Kp = 200;
int Kd = 120;
int Ki = 1;
int Ko = 50;


unsigned char moving = 0;  // is the base in motion?

/*
 * Initialize PID variables to zero to prevent startup spikes
 * when turning PID on to start moving
 * In particular, assign both Encoder and PrevEnc the current encoder value
 * See http://brettbeauregard.com/blog/2011/04/improving-the-beginner%E2%80%99s-pid-initialization/
 * Note that the assumption here is that PID is only turned on
 * when going from stop to moving, that's why we can init everything on zero.
 */
void resetPID() {
  leftPID.TargetTicksPerFrame = 0.0;
  leftPID.Encoder = readEncoder(LEFT);
  leftPID.PrevEnc = leftPID.Encoder;
  leftPID.output = 0;
  leftPID.PrevInput = 0;
  leftPID.ITerm = 0;

  rightPID.TargetTicksPerFrame = 0.0;
  rightPID.Encoder = readEncoder(RIGHT);
  rightPID.PrevEnc = rightPID.Encoder;
  rightPID.output = 0;
  rightPID.PrevInput = 0;
  rightPID.ITerm = 0;

  rearLeftPID.TargetTicksPerFrame = 0.0;
  rearLeftPID.Encoder = readEncoder(REAR_LEFT);
  rearLeftPID.PrevEnc = rearLeftPID.Encoder;
  rearLeftPID.output = 0;
  rearLeftPID.PrevInput = 0;
  rearLeftPID.ITerm = 0;

  rearRightPID.TargetTicksPerFrame = 0.0;
  rearRightPID.Encoder = readEncoder(REAR_RIGHT);
  rearRightPID.PrevEnc = rearRightPID.Encoder;
  rearRightPID.output = 0;
  rearRightPID.PrevInput = 0;
  rearRightPID.ITerm = 0;
}

/* PID routine to compute the next motor commands */
void doPID(SetPointInfo *p) {
  long Perror;
  long output;
  int input;

  // Perror = p->TargetTicksPerFrame - (p->Encoder - p->PrevEnc);
  input = p->Encoder - p->PrevEnc;
  Perror = p->TargetTicksPerFrame - input;

  /*
   * Avoid derivative kick and allow tuning changes,
   * see http://brettbeauregard.com/blog/2011/04/improving-the-beginner%E2%80%99s-pid-derivative-kick/
   * see http://brettbeauregard.com/blog/2011/04/improving-the-beginner%E2%80%99s-pid-tuning-changes/
   */
  // output = (Kp * Perror + Kd * (Perror - p->PrevErr) + Ki * p->Ierror) / Ko;

  // p->PrevErr = Perror;
  output = (Kp * Perror - Kd * (input - p->PrevInput) + p->ITerm) / Ko;

  p->PrevEnc = p->Encoder;
  output += p->output;
  // Accumulate Integral error *or* Limit output.
  // Stop accumulating when output saturates
  if (output >= MAX_PWM)
    output = MAX_PWM;
  else if (output <= -MAX_PWM)
    output = -MAX_PWM;
  else
    /*
     * allow turning changes, see http://brettbeauregard.com/blog/2011/04/improving-the-beginner%E2%80%99s-pid-tuning-changes/
     */
    p->ITerm += Ki * Perror;

  p->output = output;
  p->PrevInput = input;
}

/* Read the encoder values and call the PID routine */
void updatePID() {
  /* Read the encoders */
  leftPID.Encoder = readEncoder(LEFT);
  rightPID.Encoder = readEncoder(RIGHT);
  rearLeftPID.Encoder = readEncoder(REAR_LEFT);
  rearRightPID.Encoder = readEncoder(REAR_RIGHT);

  /* If we're not moving there is nothing more to do */
  if (!moving) {
    /*
     * Reset PIDs once, to prevent startup spikes,
     * see http://brettbeauregard.com/blog/2011/04/improving-the-beginner%E2%80%99s-pid-initialization/
     * PrevInput is considered a good proxy to detect
     * whether reset has already happened
     */
    if (leftPID.PrevInput != 0 || rightPID.PrevInput != 0 || rearLeftPID.PrevInput != 0 || rearRightPID.PrevInput != 0)
      resetPID();
    return;
  }

  /* Compute PID update for each motor */
  doPID(&leftPID);
  doPID(&rightPID);
  doPID(&rearLeftPID);
  doPID(&rearRightPID);

  /* Set the motor speeds accordingly */
  setMotorSpeeds(leftPID.output, rightPID.output, rearLeftPID.output, rearRightPID.output);
}

void setMotorSpeedsFeedback(int leftWheelTarget, int rightWheelTarget, int rearLeftWheelTarget, int rearRightWheelTarget) {
  moving = 1;
  leftPID.TargetTicksPerFrame = leftWheelTarget;
  rightPID.TargetTicksPerFrame = rightWheelTarget;
  rearLeftPID.TargetTicksPerFrame = rearLeftWheelTarget;
  rearRightPID.TargetTicksPerFrame = rearRightWheelTarget;
}

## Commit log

2025-09-11 fixed lidar not showing up
    [knight.xacro, my_controllers.yaml, ros2_control.xacro]
2025-09-13 adding imu
    [my_controllers.yaml, simple.xacro, test_ros_robot_localization_listener.yaml]
2025-09-13 odometry/filtered now received
    [gazebo_control.xacro, gazebo_control_.xacro, my_controllers.yaml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]
2025-09-14 fusion finally works in gazebo
    [my_controllers.yaml]
2025-09-15 ekf sorta works on robot
    [my_controllers.yaml, robot.urdf.xacro, ros2_control.xacro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]
2025-09-15 Added ekf compatible with Gazebo fortress -- odometry/filtered still not working
    [gazebo_control.xacro, inertial_macros.xacro, knight.xacro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]
2025-09-15 fixed imu/data
    [building_robot.sdf, dojo2024.sdf, my_controllers.yaml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]
2025-09-15 Add files via upload
    Camera setup over real time streaming protocol (RTSP)
2025-09-16 fixed gazebo fortress not moving bot (friction)
    [empty.sdf, empty_.sdf, simple.xacro]
2025-09-18 Bot moving in gazebo
    [simple.xacro]
2025-09-23 added servo service
    please test reliability first
2025-09-23 color detection files
    [gazebo_control.xacro, knight.xacro, lidar_link.stl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]
2025-09-23 added servo HW interface
    [my_controllers.yaml]
2025-09-23 cleaning up servo
    [my_controllers.yaml]
2025-09-24 added colour to servo workflow
2025-09-25 updated JKL with working gamefield and robot spawn in it at the same position all the time
    [GF.sdf, knight.xacro, my_controllers.yaml]
2025-09-26 Mapping testing
    [dojo2024.sdf, knight.xacro, robot.urdf.xacro]
2025-09-27 cleaning up
    [cart_controller.yaml, cart_controller_effort.yaml, cart_controller_position.yaml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]
2025-09-27 making things run
    [GF_.sdf, gazebo_control.xacro, knight.xacro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]
2025-09-29 Pytrees publishing to nav2
    [barrels.sdf, camera.xacro, cones.sdf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]
2025-09-29 Revert "Pytrees publishing to nav2"
    This reverts commit a25208bd5a5440edb9179bc387cc0e5ef98fcf47.
    undo
    [barrels.sdf, camera.xacro, cones.sdf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]
2025-09-29 fixing robot_localization
    [simple.xacro]
2025-09-29 updated nav2 footprint to match urdf
2025-10-04 fixed robot odom drift along Y axis
    [simple.xacro]
2025-10-07 Publish to servo multiple times
2025-10-07 footprint updated
2025-10-07 updated lidar launch file
2025-10-11 added CAD
    [2.54 mm DUPONT MALE PIN HEADER, IO, 2X20, RPi4ModelB.ipt, 2.54 mm DUPONT MALE PIN HEADER, POE, 2X2, RPi4ModelB.ipt, 2X USB2.0 PORTS, RPi4ModelB.ipt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]
2025-10-18 added schematic
2025-10-19 update schematic
